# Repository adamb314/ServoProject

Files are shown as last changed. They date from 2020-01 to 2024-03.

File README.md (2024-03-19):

# ServoProject
by Adam Bäckström
### Getting the most out of your hobby servo

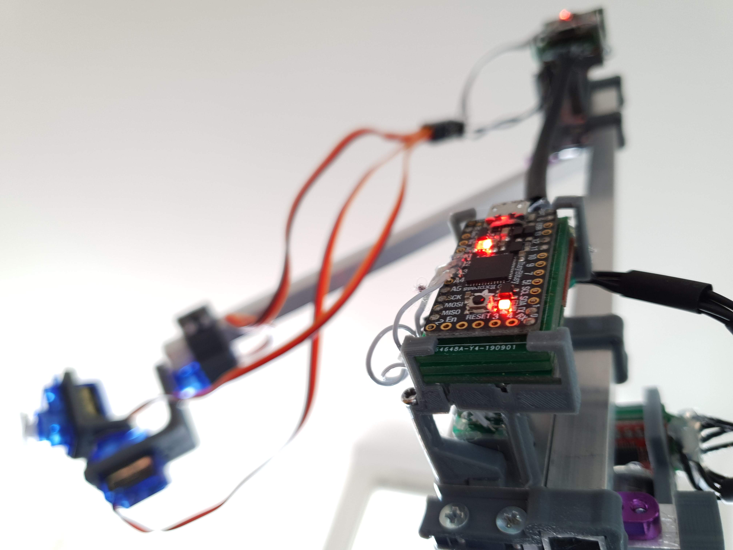
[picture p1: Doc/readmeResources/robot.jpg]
Robot


Video demo of project
---------------------

Demo video (https://www.youtube.com/watch?v=ECLrLupFW10)

Additional documentation for the project
----------------------------------------

[Theory](Doc/Theory.md)

[Dependencies](Doc/Dependencies.md)

#### Build instructions

 * [DS3225 Servo](Doc/BuildInstructionsServoDS3225.md)

 * [MG90S Micro servo](Doc/BuildInstructionsMicroServoMG90S.md)

 * [Part list for robot and gripper](Doc/PartListForRobotAndGripper.md)

 #### Legacy build instructions

   * [Brushed servo](Doc/legacy/BuildInstructionsBrushedServo.md)

   * [Coreless servo](Doc/legacy/BuildInstructionsCorelessServo.md)

   * [Micro servo](Doc/legacy/BuildInstructionsMicroServo.md)

Project structure
----------------

### ArduinoSketch

This folder contains the Arduino project for the Adafruit ItsyBitsy M0 Express boards.

Easiest way to program and configure the servos is through the configurationWizard.py script.
Just run `python3 ./ArduinoSketch/configurationWizard.py` to get started. The script will ask if it should install any missing dependencies.

PLEASE NOTE!
Windows users must use MSYS2 due to the the PyGObject package, see https://pygobject.readthedocs.io/en/latest/getting_started.html. After installing MSYS2 run the script with:
```
C:\msys64\mingw64\bin\python.exe ArduinoSketch\configurationWizard.py
```

#### Manually compiling the Arduino sketch

When compiling, the active configuration is selected by modifying the `#include "*.h"` line in the `config/config.h` file to include the desired config file. The `configSelector.py` script can be used to simplify the config selecting process by giving a drop-down list with all configs in the config folder.

The folder also holds a Makefile which can be used to compile and transfer the project. One benefit of using the Makefile is that the configSelector script is always executed prior to compiling. To be able to use the Makefile you must first install arduino-cli.

```
Arduino sketch dependencies:
  - Adafruit DotStar `source:` Arduino Library List
  - Eigen `source:` Arduino Library List
```

### ArduinoLibrary/ServoProjectController

Arduino library for communicating with the servos.

[View Example Arduino sketch](ArduinoLibrary/ServoProjectController/examples/ArduinoDemo/ArduinoDemo.ino)

### C++/Library

Holds the C++ library for communicating with the servos.
```
Dependencies:
  - GNU Make >= 4.2.1
  - gcc >= 9.3.0
  - boost >= 1.71.0
```

#### C++/Demo

Minimal c++ demo project.

[View Example Code](C++/Demo/src/main.cpp)

#### C++/Example6dofRobot

Example 6dof robot project.

[View Example Code](C++/Example6dofRobot/src/main.cpp)

To compile run `make`. This creates the program `./executable` with the following options.

```
Allowed options:
  --playPath            play the path defined in createPath()
  --gui                 open jogging gui
  --output arg          data output file
  --simulate            simulate servos

```
```
Dependencies:
  - Eigen >= 3.4.0
  - gtkmm-3.0 >= 3.24
```

### CadFiles

Holds all `.stl` and the original Freecad files

### PcbDesignes

Holds all KiCad projects for the electronics

### Python/Demo

Python demo project.

[View Example Code](Python/demo.py)

### Python/ServoProjectModules

Holds all python modules for the project.

Communication bus setup for demo projects
-----------------------------------------

#### ONLY CONNECT THE SERVO TO 3.3V LOGIC!!!!

Robot

PLEASE NOTE! The bus controller needs to have a low latency to get fast communication with the servos. Most standard USB to Serial converters buffer the data and only transfers every 10 ms or so. This becomes a problem since the communication protocol will wait for the response from each servo before moving on to the next, adding huge delays.

To get the best communication speed it is recommended to use an "Adafruit ItsyBitsy M0 Express" (or similar ARM based Arduino) as the USB to Serial converter. Just program the Arduino with the `usbToSerial.h` configuration in the ArduinoSketch to get started. In `usbToSerial.h` you can also configure any regular servos you want to control together with the ServoProject modified ones.

How to switch to PWM interface version
--------------------------------------

#### ONLY CONNECT THE SERVO TO 3.3V LOGIC!!!!

Using the PWM interface is not recommended due to low resolution and high noise, but it is possible by modifying the configuration file. To enable PWM control replace the `getCommunicationHandler()` function with the version below.

```
    static std::unique_ptr<Communication> getCommunicationHandler()
    {
        Serial.begin(115200);
        auto com = std::make_unique<Communication>(SerialComOptimizer(&Serial));
        uint8_t pwmPin = 0; // Rx pin, ONLY CONNECT TO 3.3V LOGIC!!!!
        uint8_t controlSpeed = 14;
        uint8_t backlashControlSpeed = 2;
        float scale = 2.0f; // 2 units per us (4096 units == 360 deg)
        float offset = 1024.0f; // move to 1024 units (90 deg) for 1500 us pwm signal
        com->addCommunicationNode(
                std::make_unique<DCServoCommunicationHandlerWithPwmInterface>(1,
                    createDCServo<SetupConfigHolder>(controlSpeed, backlashControlSpeed),
                    pwmPin, scale, offset));
        return com;
    }
```

License
-------

Open Source License

ServoProject is free software. You can redistribute it and/or modify it under the terms of Creative Commons Attribution 3.0 United States License.

To view a copy of this license, visit
http://creativecommons.org/licenses/by/3.0/us/

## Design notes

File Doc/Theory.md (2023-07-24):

Theory
------

## PID vs Cascade control

The control system of a regular hobby servo looks something like this:

loop1

This control scheme is good at holding and moving fast between position, but not so good at following a smooth predefined motion. Which is what you want when you build a robot.

Industrial servo controllers use a cascade based control scheme instead, which looks something like this:

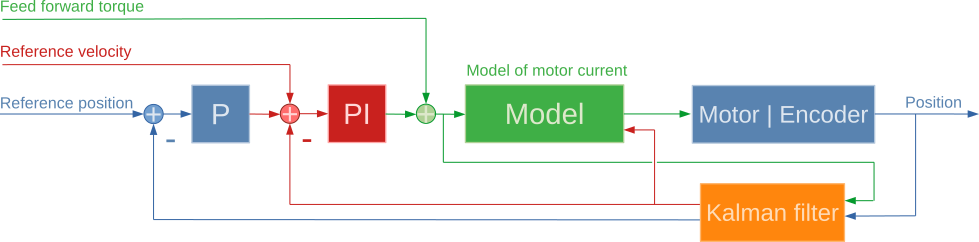
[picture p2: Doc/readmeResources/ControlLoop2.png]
loop2


This is the control scheme used in this project.

The main benefit of this approach is that it also takes the velocity and torque into account. This allows for a much tighter motion tracking.

## Backlash control

When dealing with cheap gearboxes, backlash is always a problem. The hacked servos in this project uses two encoders to compensate for backlash. One AS5048a magnetic encoder or a potentiometer on the output shaft and one custom optical encoder inside the DC-motor. The benefit of having the extra encoder inside the motor is getting higher resolution and a main control loop which is backlash free. If one would only use the AS5048a for controlling, the backlash would enter the control loop as a time delay. This limits the control loop performance.

The backlash compensation is done by moving the motor position control loops reference-position so that the output encoder reaches the correct position.

## The complete control loop

The following diagram shows the full control loop design used in this project:

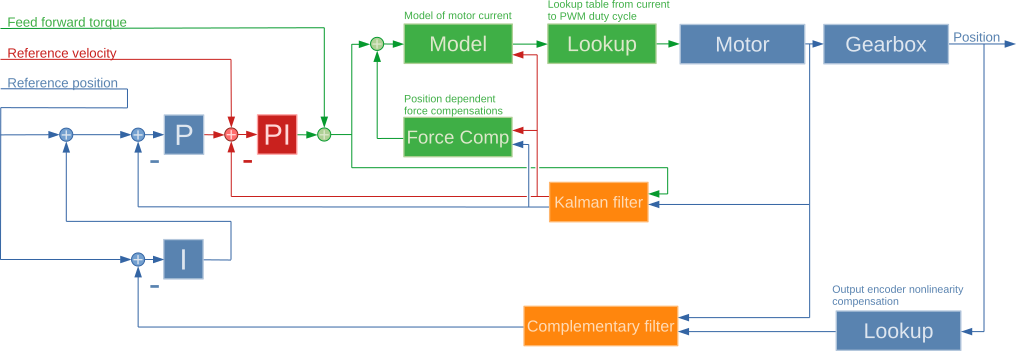
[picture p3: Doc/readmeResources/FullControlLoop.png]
fullLoop


It consists of three cascade control levels:
1) Backlash control loop
2) Motor position control loop
3) Motor velocity control loop

Apart from these three feedback loops there are four model/open-loop based compensation steps based on:
1) Velocity based motor current model (see CurrentControlModel class in `ArduinoSketch/src/Control/CurrentControlLoop.cpp`)
2) PWM duty cycle based motor current model (lookup table based, see `ArduinoSketch/src/Hardware/PwmHandler.cpp`)
3) Motor position based force compensation (see `ArduinoSketch/src/Control/DCServo.cpp` function `applyForceCompensations`)
4) Output encoder nonlinearity model

For the exact implementation see the `controlLoop()` function in `ArduinoSketch/src/Control/DCServo.cpp`.

## System identification

To be able to calculate the parameters of the control loops we need to have a mathematical model of the servo. This is handled by the python module `SystemIdentification.py`. First step is to record the position-time-series of the motor for a sequence of PWM values with random sign. The sequence starts with the highest PWM value, in the test range, and moves down towards the lowest, in discrete steps. Next the velocity is calculated from the position-time-series. For each part, with the same absolute PWM value, the velocity change will follow this equation:

$$ v_{k+1} = a v_k + b u_k - c_f sign(v_k) $$

where $u_k$ is $\pm$ the PWM value and $c_f$ is the friction constant. By only considering the parts where

$$ sign(v_k) = sign(u_k) $$

we can bake in $c_f$ into $b$ resulting in:

$$ v_{k+1} = a v_k + b^{'} u_k $$

The parameters $a$ and $b^{'}$ are then estimated with the least squares method. After that their continuous time equivalent values $a_{cont}$ and $b_{cont}$ are calculated.

How $b_{cont}$ varies over the PWM range is then used to calculate the PWM nonlinearity and the linear trend of $a_{cont}$ is used to calculate the $c_{EMF}$ value of the motor.

After this we add friction to the model and simulate the response. The final friction $c_{fric}$ is calculated by minimizing the error between the model and the real system.

The final model looks like this:

$$ \frac{dv}{dt} = a_{cont} v(t) + b_{cont} pwmNonlin(u(t)) + c_{fric} sign(v(t)) + c_{EMF} abs(pwmNonlin(u(t))) v(t) $$

## Calculating the control parameters
This project uses pole placement to calculate the control parameters for the cascade controllers. To get the equations for the poles we need to find the closed transfer functions for the velocity and position control loops.

### Transfer function of open system to closed system
Given the discrete transfer function for the open system:

$$ G_0(z)=\frac{p(z)}{q(z)} $$

where $p(z)$ and $q(z)$ are pure polynomials, we can derive the closed system's transfer function as follows:

$$ Y = G_0(z) (R - Y) \iff Y = \frac{G_0(z)}{1 + G_0(z)} R = \frac{p(z)}{p(z) + q(z)}R $$

Which gives us the closed system transfer function

$$ G_c(z) = \frac{p(z)}{p(z) + q(z)} $$

### Position control loop

The position control loop's open transfer function consists of a proportional gain controller and an integrator (we approximate the inner velocity loop as a pure integrator):

$$ G_0(z)=G_{posControl}(z) G_{velLoop}(z)= (L_0) (\frac{dt}{z - 1}) $$

This gives us $p(z) = L_0 dt$ and $q(z) = z - 1$ which means that the pole polynomial is:

$$ p(z) + q(z) = z - 1 + L_0 dt $$

with the root:

$$ z - 1 + L_0 dt = 0 \iff z_{posPole} = 1 - L_0 dt $$

which means that the position control loop gain $L_0$ can be calculated with:

$$ L_0 =\frac{1 - z_{posPole}}{dt} $$

### Velocity control loop

The velocity control loop's open transfer function consists of a PI controller and the motor's transfer function (from control signal to velocity) which we approximate as a first order damped system:

$$ G_0(z)=G_{velControl}(z) G_{motor}(z)= (L_1 + L_2 \frac{1}{z - 1})(\frac{b}{z - a}) $$

This gives us $p(z) = b (L_1 (z - 1) + L_2)$ and $q(z) = (z - 1)(z - a)$ which means that the pole polynomial is:

$$ p(z) + q(z) = b (L_1 (z - 1) + L_2) + (z - 1)(z - a) = (a - b L_1 + b L_2) + (b L_1 -a - 1) z + z^2 $$

Substituting in $L_1^{'} = b L_1$ and $L_2^{'} = b L_2$ gives us:

$$ (a - L_1^{'} + L_2^{'}) + (L_1^{'} -a - 1) z + z^2 $$

with the roots:

$$ z_{velPole} = 1/2 (±\sqrt{{L_1^{'}}^2 + (1 - a) ((1 - a) + 2 L_1^{'}) - 4 L_2^{'}} + a - L_1^{'} + 1) $$

Given that we want the closed loop system to be stable and at least as fast as the open loop ($z_{openLoopPole} = a$) we can deduce the following:

$$ 0 < 1/2 (a - L_1^{'} + 1) \le a \le 1  \iff $$

$$ 0 < a - L_1^{'} + 1 \le 2a, \space 0 < a \le 1 \Rightarrow $$

$$ 0 \le 1 - a \le L_1^{'} < a + 1 \le 2 $$

To get a damped system we need real roots $\Rightarrow$

$$ {L_1^{'}}^2 + (1 - a) ((1 - a) + 2 L_1^{'}) - 4 L_2^{'} \ge 0 $$

since $0 < a \le 1$ and $L_1^{'} > 0 \Rightarrow$

$$ {L_1^{'}}^2 + (1 - a) ((1 - a) + 2 L_1^{'}) - 4 L_2^{'} \ge 
 {L_1^{'}}^2 - 4 L_2^{'} \ge 0 $$

Substituting back to $L_1$ and $L_2$ results in:

$$ b (b L_1^2 - 4 b L_2) \ge 0 \iff b L_1^2 \ge 4 L_2 $$

If $L_1$ and $L_2$ are calculated so that

$$ {L_1^{'}}^2 - 4 L_2^{'} = 0 $$

then an increase of the load inertial on the motor ($b^{'} < b$) will result in an undamped system. To prevent this we can introduce an inertial margin $c_{im}$ such that $b^{'} = b / c_{im} \le b$. We want the damped system inequality to hit the limit if $b$ changes to $b^{'}$. This yields the following:

$$ (a - 1)^2 - 2 a L_1^{'} / c_{im} + (L_1^{'} / c_{im})^2 + 2 L_1^{'} / c_{im} - 4 L_2^{'} / c_{im} = 0 \iff $$

$$ L_2^{'} = 1/4 (c_{im} (a - 1)^2 - 2 a L_1^{'} + {L_1^{'}}^2 / c_{im} + 2 L_1^{'}) = $$

$$ = L_2^{'} = 1/4 ({L_1^{'}}^2 / c_{im} + (a - 1) (c_{im} (a - 1) - 2 L_1^{'})) $$

The slowest pole of a system is the one that affect the speed of the system the most and a discrete pole is slower the closer to the value one it is. Since both of the velocity poles should satisfy

$$ 0 < z_{velPole} \le a $$

we should place the largest pole of the two:

$$ z_{velPole} = 1/2 (\sqrt{{L_1^{'}}^2 + (1 - a) ((1 - a) + 2 L_1^{'}) - 4 L_2^{'}} + a - L_1^{'} + 1) $$

substituting in $L_2^{'}$

$$ z_{velPole} = 1/2 (\sqrt{{L_1^{'}}^2 + (1 - a) ((1 - a) + 2 L_1^{'}) - {L_1^{'}}^2 / c_{im} - (1 - a) (c_{im} (1 - a) + 2 L_1^{'})} + a - L_1^{'} + 1) = $$

$$ = z_{velPole} = 1/2 (\sqrt{(1 - 1 / c_{im}) {L_1^{'}}^2 + (1 - a) ((1 - a) + 2 L_1^{'} - c_{im} (1 - a) - 2 L_1^{'})} + a - L_1^{'} + 1) = $$

$$ = z_{velPole} = 1/2 (\sqrt{(1 - 1 / c_{im}) {L_1^{'}}^2 + (1 - a)^2 (1- c_{im})} + a - L_1^{'} + 1) \Rightarrow $$

$$ L_1^{'} = c_{im} (a - 2 z_{velPole} + 1) + 2 \sqrt{c_{im} (c_{im} - 1) (1 - z_{velPole}) (a - z_{velPole})} $$

Resulting in the final equations:

$$ L_1^{'} = c_{im} (a - 2 z_{velPole} + 1) + 2 \sqrt{c_{im} (c_{im} - 1) (1 - z_{velPole}) (a - z_{velPole})} $$

$$ L_2^{'} = 1/4 ({L_1^{'}}^2 / c_{im} + (a - 1) (c_{im} (a - 1) - 2 L_1^{'})) $$

$$ L_1 = L_1^{'} / b $$

$$ L_2 = L_2^{'} / b $$

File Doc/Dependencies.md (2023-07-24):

Dependencies
------------

#### ArduinoSketch/configSelector.py
* Python >= 3.8.2
* python3-gi

#### ArduinoSketch/configurationWizard.py
* Python >= 3.8.2
* python3-gi

* matplotlib >= 3.4.2
* numpy >= 1.17.4
* pyserial >= 3.5
* requests >= 2.22.0
* scipy >= 1.7.0

#### ArduinoSketch/Makefile
* GNU Make >= 4.2.1
* arduino-cli

#### C++/Demo
* GNU Make >= 4.2.1
* gcc >= 9.3.0
* boost >= 1.71.0

#### C++/Example6dofRobot
* GNU Make >= 4.2.1
* gcc >= 9.3.0
* boost >= 1.71.0
* Eigen >= 3.4.0
* gtkmm-3.0 >= 3.24

#### C++/Library
* GNU Make >= 4.2.1
* gcc >= 9.3.0
* boost >= 1.71.0

#### Python/demo.py
* Python >= 3.8.2
* numpy >= 1.17.4
* pyserial >= 3.5

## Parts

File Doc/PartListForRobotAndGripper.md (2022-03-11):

Gripper
--------

* 1 x SG90 servo

".stl" files for 3D printing:
```
CadFiles/Robot/stl/GripperBase.stl
CadFiles/Robot/stl/GripperClip.stl
CadFiles/Robot/stl/GripperFinger1.stl
CadFiles/Robot/stl/GripperFinger2.stl
CadFiles/Robot/stl/GripperMount.stl
```

Robot
--------

* 3 x Modified coreless servo
* 3 x Modified micro servo
* 1 x Gripper
* 1 x 10 x 10 mm square aluminum bar (about 500 mm)
* 1 x 15 x 15 mm square aluminum bar (about 100 mm)
* 1 x 5V Powersuply 
* 1 x Fast USB to serial microcontroller (Adafruit ItsyBitsy M0 Express or Arduino MKR Zero)
  * https://learn.adafruit.com/introducing-itsy-bitsy-m0
  * https://store.arduino.cc/arduino-mkr-zero-i2s-bus-sd-for-sound-music-digital-audio-data

Cad and stl files for 3D printing:
```
CadFiles/Robot
```

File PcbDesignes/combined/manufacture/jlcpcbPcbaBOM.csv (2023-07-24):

Comment | Designator | Footprint | LCSC Part #
10uF | C1 C3 |  | C15525
1uF | C4 C5 |  | C52923
LED | D1 |  | C84256
D | D2 D3 |  | C64898
120 | R1 R2 |  | C25079
8.2k | R3 R5 |  | C25924
100k | R4 |  | C25741
2.2k | R6 |  | C25924
AP2112K-3.3 | U3 |  | C51118
ATSAMD21G18A-A | U4 |  | C78624
TB6612FNG | U5 |  | C88224
USB_B_Micro | USB1 |  | C132563

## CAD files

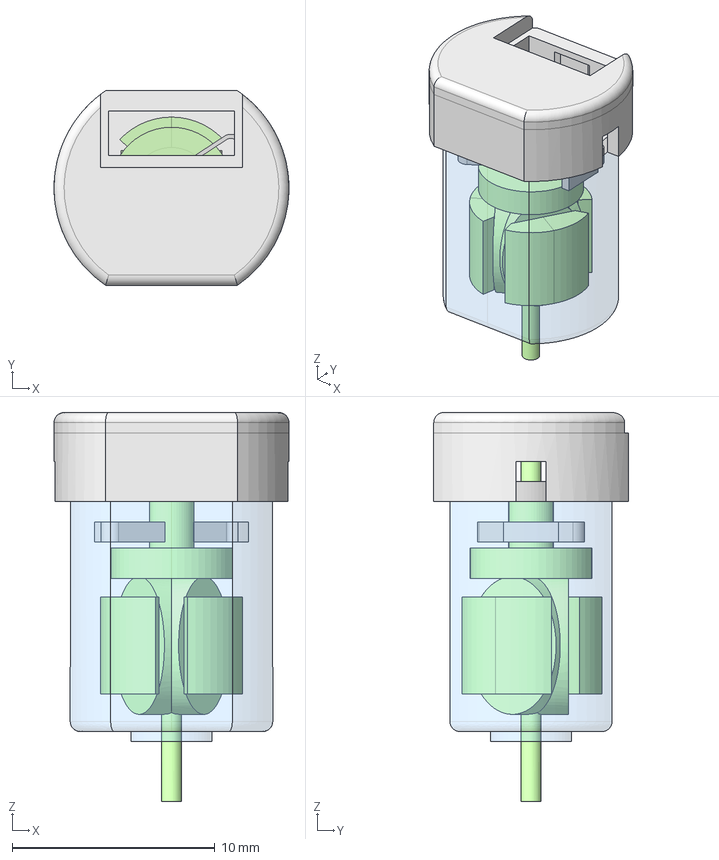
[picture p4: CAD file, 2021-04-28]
CadFiles/MicroServo/MicroServoAssembly.FCStd
11.6 x 9.60 x 19.2 mm
sensorMount

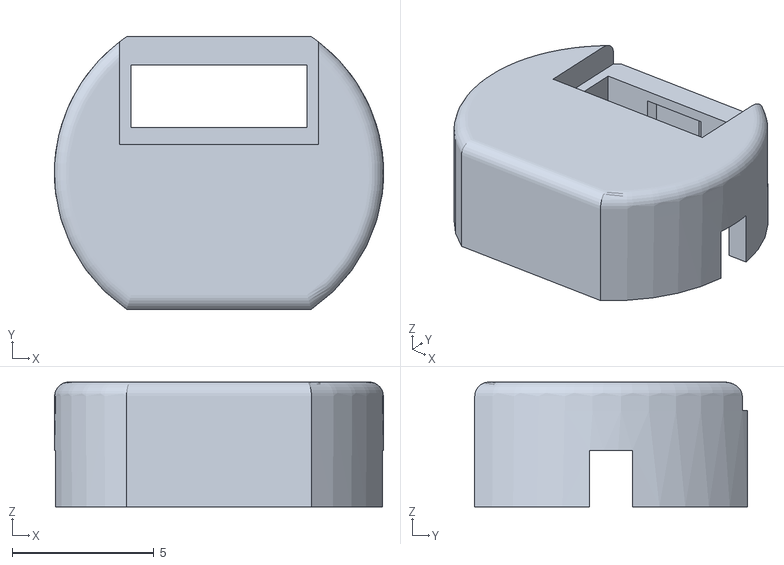
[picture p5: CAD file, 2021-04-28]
CadFiles/MicroServo/stl/OpticalEncoderSensorMount.stl
11.6 x 9.60 x 4.40

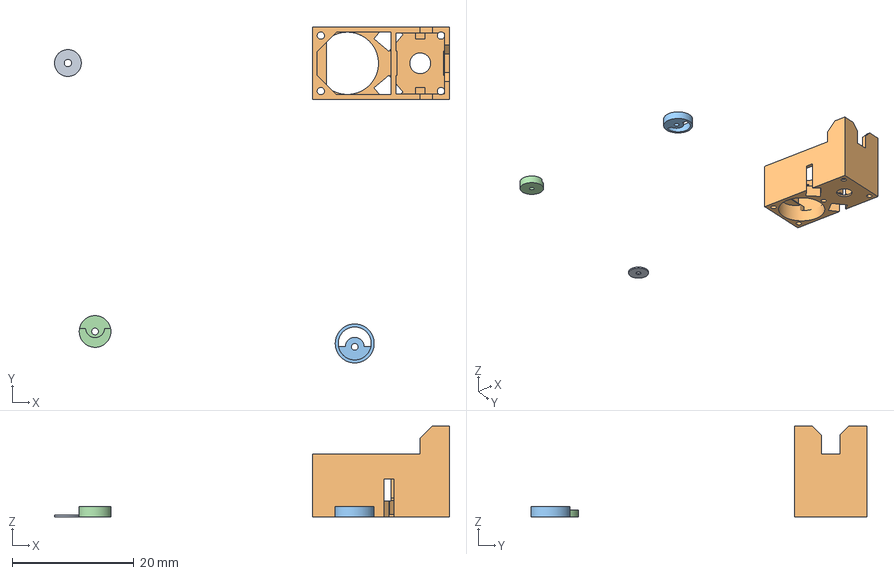
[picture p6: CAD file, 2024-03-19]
CadFiles/MicroServoMG90S/prusaSlicer.3mf
64.8 x 55.1 x 14.9 mm
baseBushings.stl
baseBox.stl
encDisc(white).stl
encDiscTruningMount(white).stl

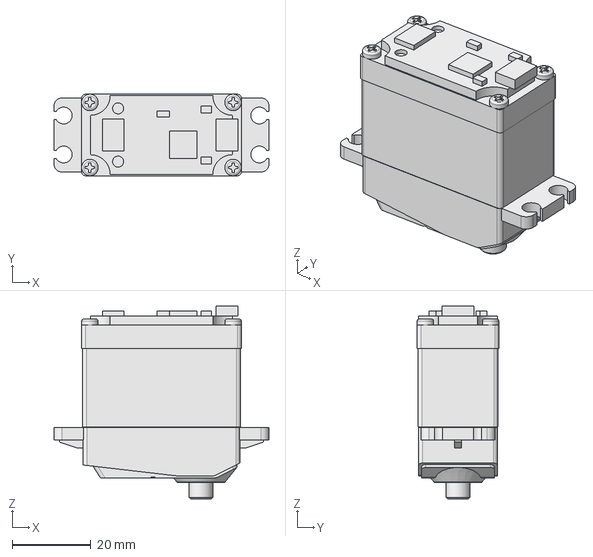
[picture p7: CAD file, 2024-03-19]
CadFiles/Robot/brushedServo.step
54.5 x 20.7 x 48.9 mm

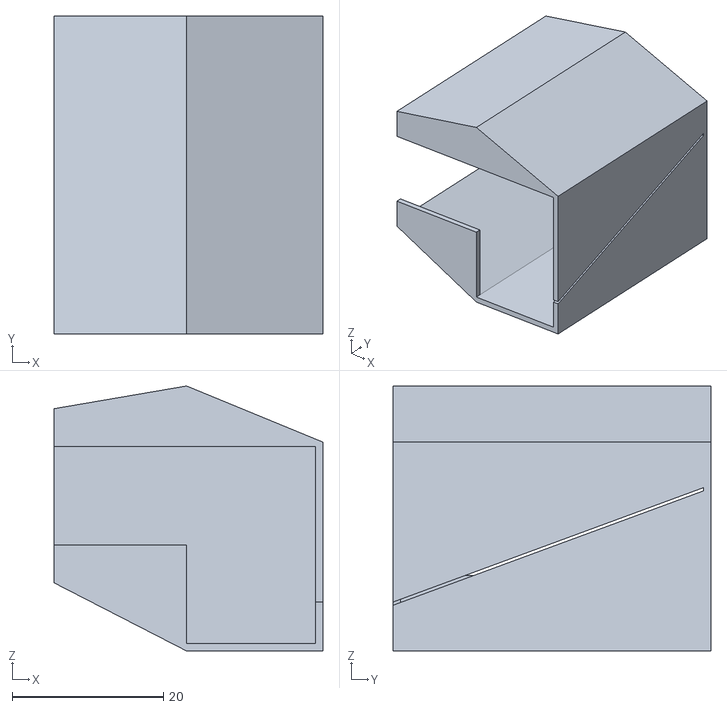
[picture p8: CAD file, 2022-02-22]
CadFiles/Robot/stl/s3Cover.stl
35.5 x 42.0 x 35.0

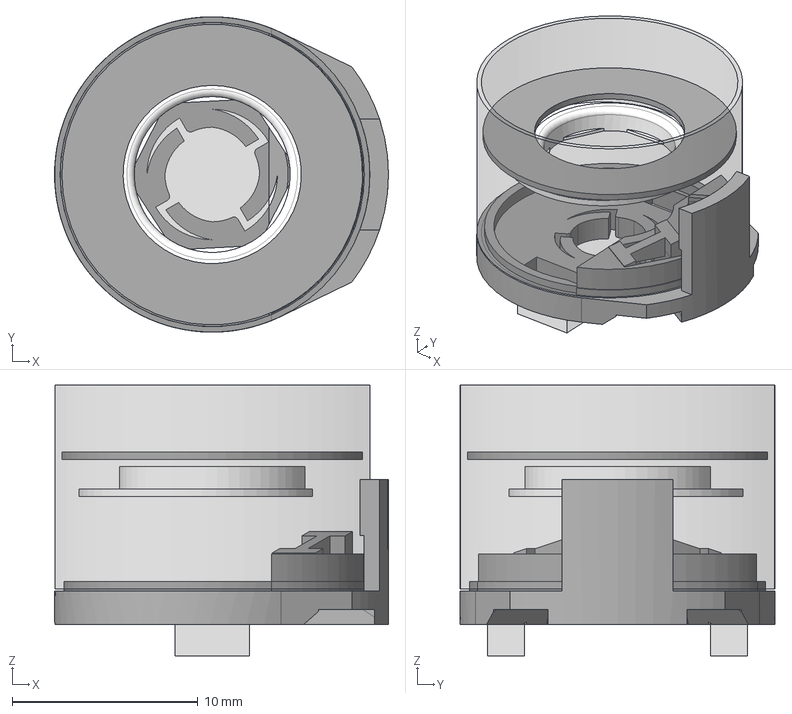
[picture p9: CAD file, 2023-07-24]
CadFiles/ServoBrushed/motor.FCStd
18.0 x 17.0 x 14.6 mm
motorPart1
motorPart2
sensor1
sensor2
EncoderDiscWhite
EncoderDiscBlack
MotorLid

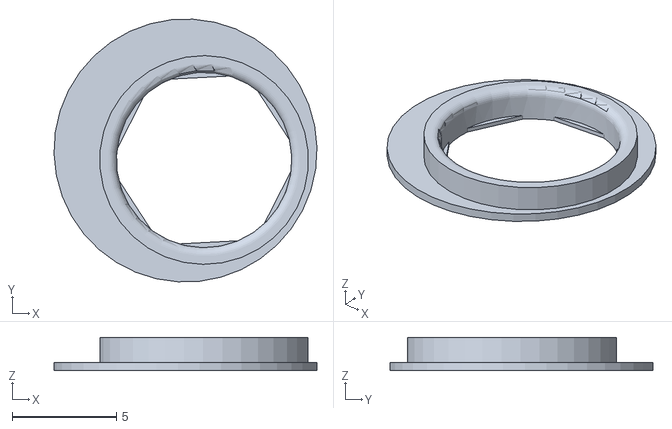
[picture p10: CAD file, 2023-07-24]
CadFiles/ServoBrushed/stl/EncDiscWhite.stl
12.6 x 12.6 x 1.60

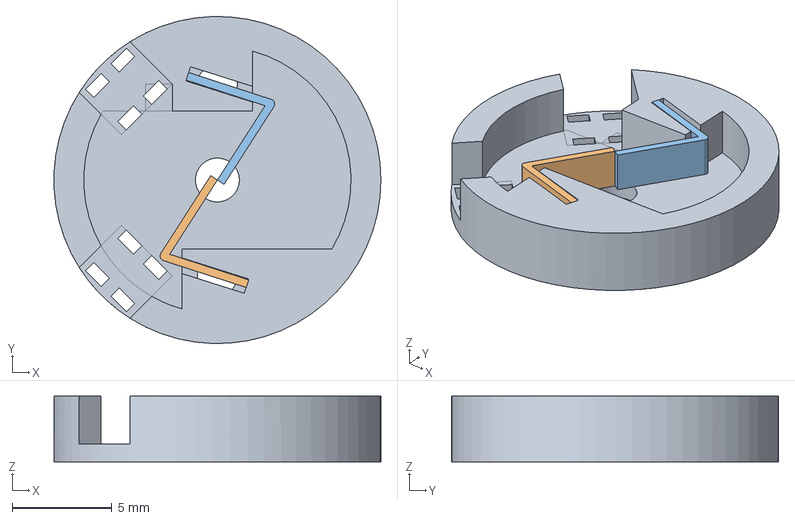
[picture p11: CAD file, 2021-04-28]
CadFiles/ServoCoreless/motorLid.FCStd
16.4 x 16.4 x 3.30 mm
Lid

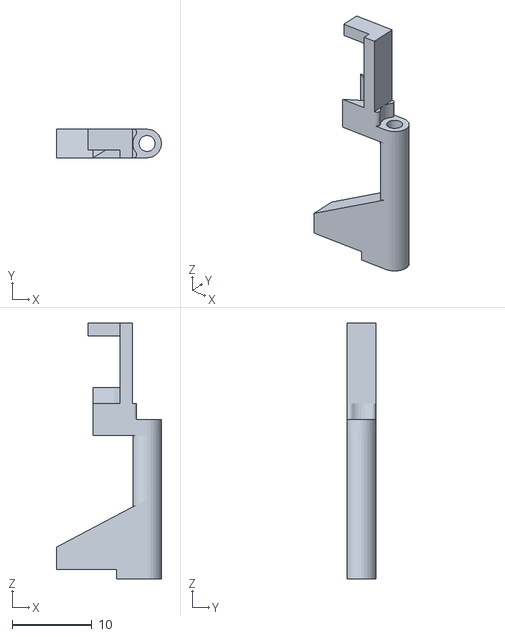
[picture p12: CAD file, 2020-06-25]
CadFiles/ServoCoreless/stl/pcbMount-part3.stl
13.2 x 3.60 x 32.1

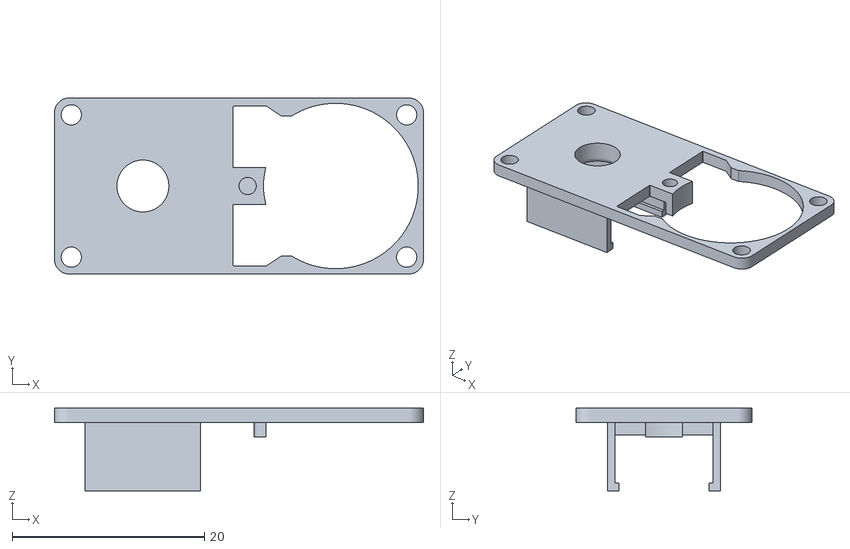
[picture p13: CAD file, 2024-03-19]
CadFiles/ServoDS3225/gearLidBottom.stl
38.4 x 18.3 x 8.60

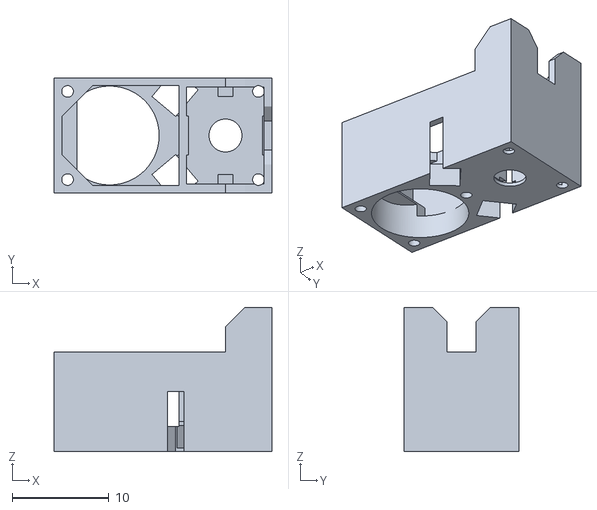
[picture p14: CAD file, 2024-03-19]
CadFiles/MicroServoMG90S/baseBox.stl
22.5 x 11.9 x 14.9

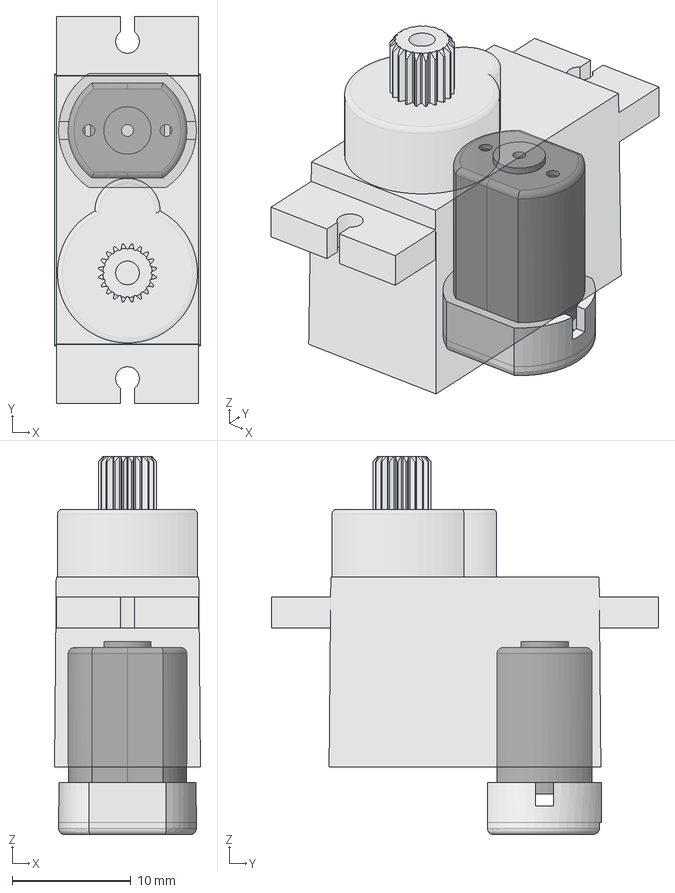
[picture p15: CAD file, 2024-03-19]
CadFiles/Robot/microServo.step
12.3 x 32.6 x 31.9 mm

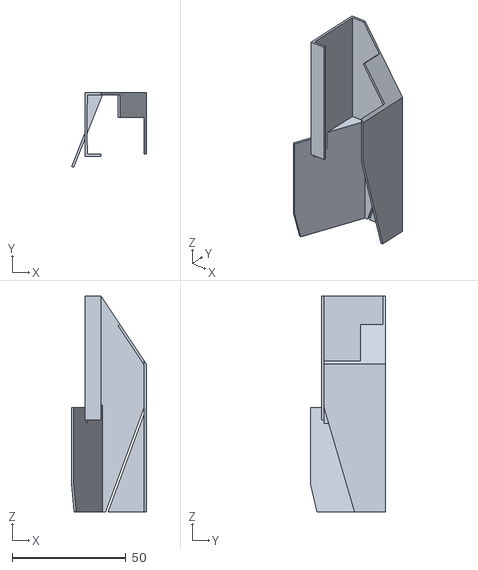
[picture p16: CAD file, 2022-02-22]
CadFiles/Robot/stl/s4Cover.stl
32.9 x 32.9 x 95.0

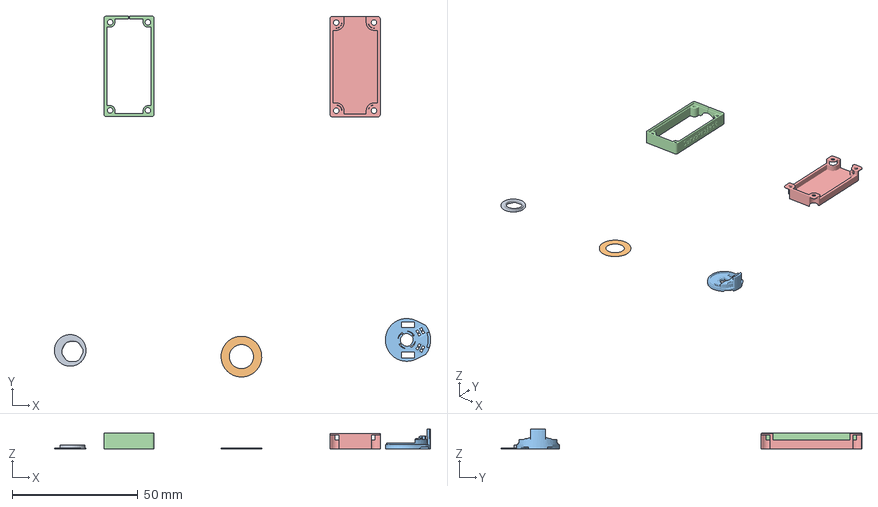
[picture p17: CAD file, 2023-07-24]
CadFiles/ServoBrushed/PrusaMiniPrintProject.3mf
149.5 x 143.4 x 7.80 mm
EncDiscWhite.stl
EncDiscBlack.stl
motorLid.stl
backCover.stl
backCoverTransparent.stl

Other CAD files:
CadFiles/ServoBrushed/stl/motorLid.stl
CadFiles/ServoCoreless/pcbMount.FCStd
CadFiles/ServoCoreless/stl/pcbMount-part2.stl
CadFiles/ServoDS3225/pcbMount.stl
CadFiles/MicroServoMG90S/baseBushings.stl
CadFiles/MicroServoMG90S/encDisc.stl
CadFiles/MicroServoMG90S/encDiscTruningMount.stl
CadFiles/Robot/brushedServoHorn.step
CadFiles/Robot/stl/GripperBase.stl
CadFiles/Robot/stl/GripperClip.stl
CadFiles/Robot/stl/GripperFinger1.stl
CadFiles/Robot/stl/GripperFinger2.stl
CadFiles/Robot/stl/GripperMount.stl
CadFiles/Robot/stl/ServoBigMagEnc.stl
CadFiles/Robot/stl/ServoBigMagEncMagHold.stl
CadFiles/Robot/stl/ServoBigMount.stl
CadFiles/Robot/stl/ServoBigMountMirrored.stl
CadFiles/Robot/stl/midS2S3Cover.stl
CadFiles/Robot/stl/s1Cover.stl
CadFiles/Robot/stl/s4Bushing.stl
CadFiles/Robot/stl/s4Mount.stl
CadFiles/Robot/stl/s5Bushing.stl
CadFiles/Robot/stl/s5Cover.stl
CadFiles/Robot/stl/s5CoverP2.stl
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

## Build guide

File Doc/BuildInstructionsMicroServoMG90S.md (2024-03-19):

## Part list

* WS-MG90S micro servo
* 2 x ITR8307
* Custom PCB
* Flat cables
    * 2 leads wide
    * 3 x 3 leads wide
    * 4 leads wide
* pin header 1x4
* 3D printed parts
    * baseBox
    * baseBushing
    * encDisc
    * encDiscTurningMount

## Build instructions

### Prepare parts

1. Order PCB using gerber, BOM and CPL files:
    - `PcbDesignes/combined/manufacture/gerber.zip`
    - `PcbDesignes/combined/manufacture/jlcpcbPcbaBOM.csv`
    - `PcbDesignes/combined/manufacture/jlcpcbPcbaCPL.csv`

2. Burn bootloader to PCB with a Raspberry Pi

    Power PCB via USB from pi and connect:
    ```
        Prog1:D (swdio) -> GPIO 25
        Prog1:C (swclk) -> GPIO 11
        Prog1:Reset     -> 3.3v

        (GPIO nr are for a Raspberry Pi 3 B)
    ```

     1. Install OpenOCD on the pi with this guide:
           https://learn.adafruit.com/programming-microcontrollers-using-openocd-on-raspberry-pi/compiling-openocd
        
        or using apt-get:
        ```
           sudo apt-get install openocd
        ```
    
     2. Download bootloader:
           https://github.com/adafruit/uf2-samdx1/releases/download/v3.13.0/bootloader-itsybitsy_m0-v3.13.0.bin
    
        or latest from:
           https://github.com/adafruit/uf2-samdx1/releases
          
     3. Put \*.bin file in new folder on pi together with the file [burnBootloaderWithOpenOCD.txt](../PcbDesignes/burnBootloaderWithOpenOCD.txt) and rename the script file to `openocd.cfg`

     4. run:
        ```
           cd \\|Insert name of folder on pi with the script
           sudo openocd
        ```

3. Print objects in PrusaSlicer project file `CadFiles/MicroServoMG90S/prusaSlicer.3mf`
    
    Print in black PLA:
    - `baseBox.stl`
    - `baseBushings.stl`

    Print in white PLA:
    - `encDisc.stl`
    - `encDiscTurningMount.stl`

### Modify the servo

Modify the servo according to the [Build Video](https://youtu.be/VcU6IY8n05g?t=0)

Build Video (https://youtu.be/VcU6IY8n05g?t=0)

Build steps in video:

1. Disassemble the servo

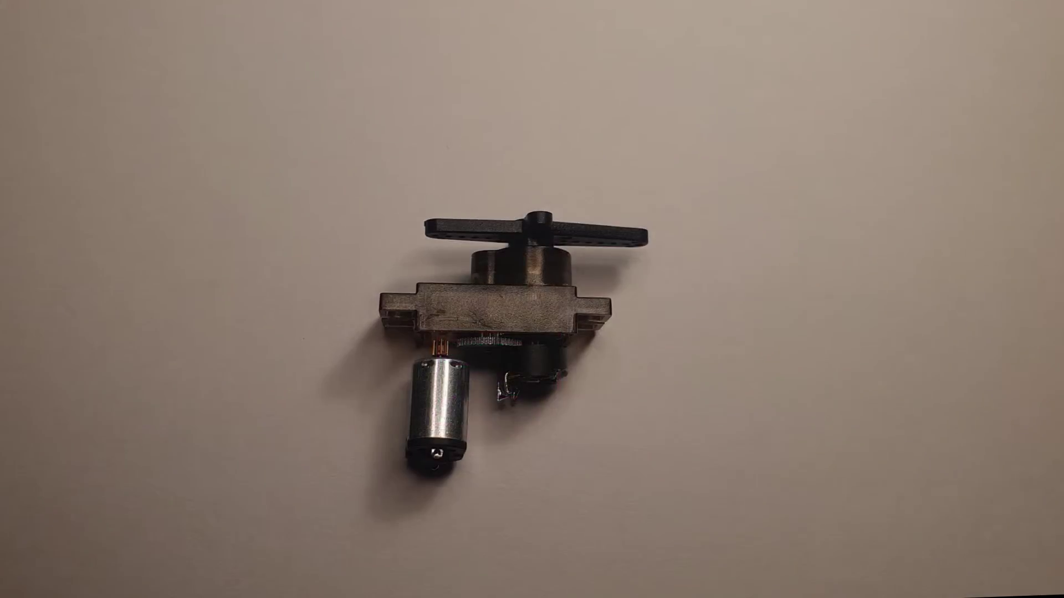
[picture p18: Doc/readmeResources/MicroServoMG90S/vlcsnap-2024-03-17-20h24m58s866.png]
    

2. The `encDisc` part has to  be completely smooth and free from defects. Getting the required resolution out of a normal FDM 3D printer is basically impossible. So to get a smooth `encDisc` part we first need to file it down while spinning it:

    1. Remove the gear from the motor and mount `encDiscTurningMount` on motor axis. Then mount `encDisc` on `encDiscTurningMount`

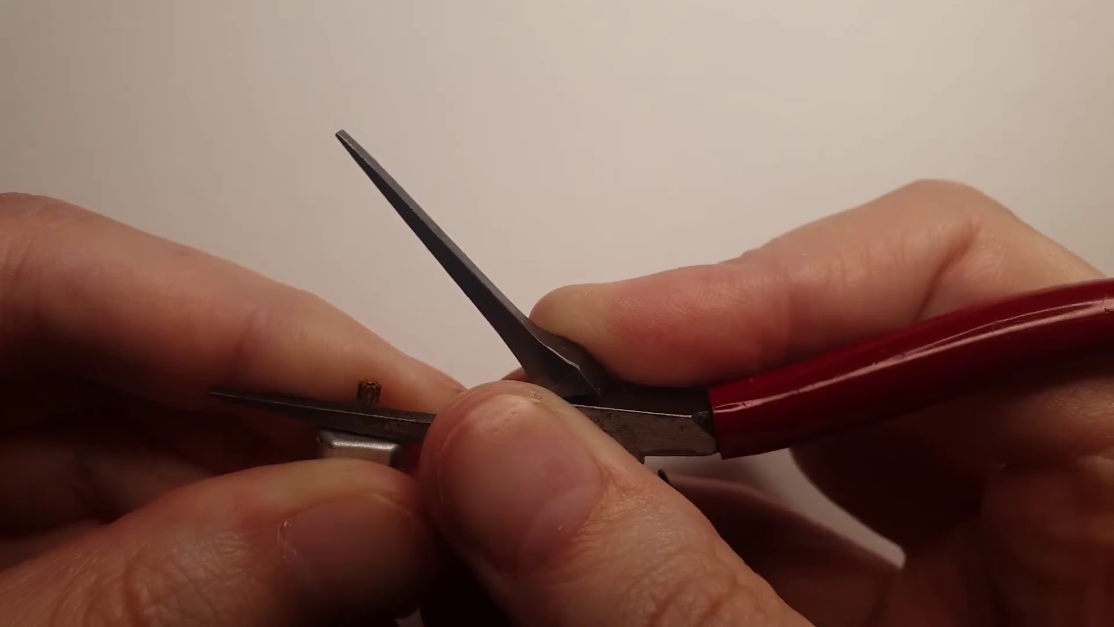
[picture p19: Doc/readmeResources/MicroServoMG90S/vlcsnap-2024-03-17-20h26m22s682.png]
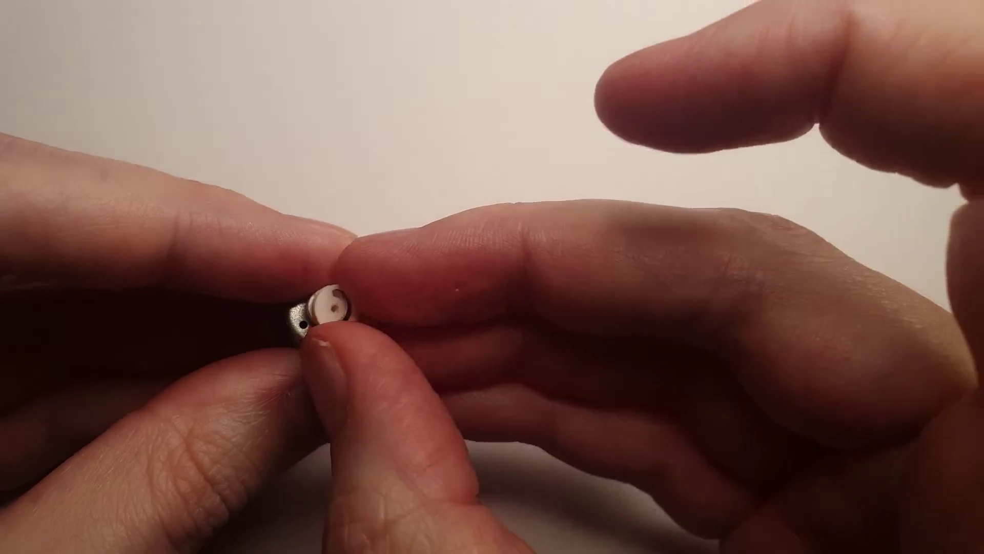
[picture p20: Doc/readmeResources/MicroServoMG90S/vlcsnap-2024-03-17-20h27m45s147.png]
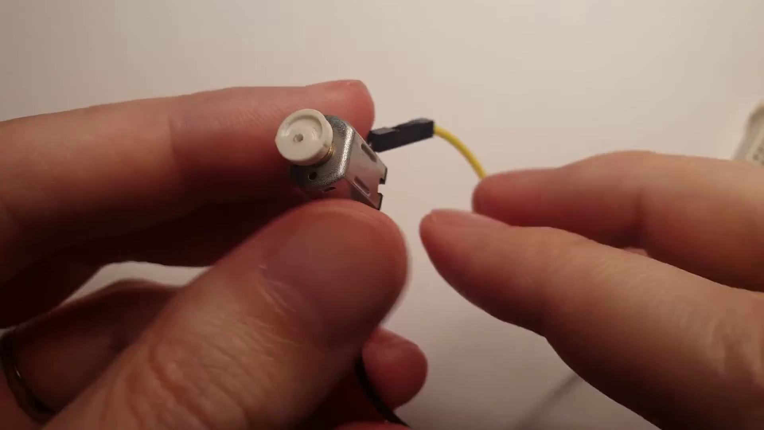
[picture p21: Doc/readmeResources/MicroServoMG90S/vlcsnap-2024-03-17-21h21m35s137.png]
          

    2. Apply 3-5 volts to the motor and file down 3D printing seams and printing lines until the surface of `encDisc` is completely smooth

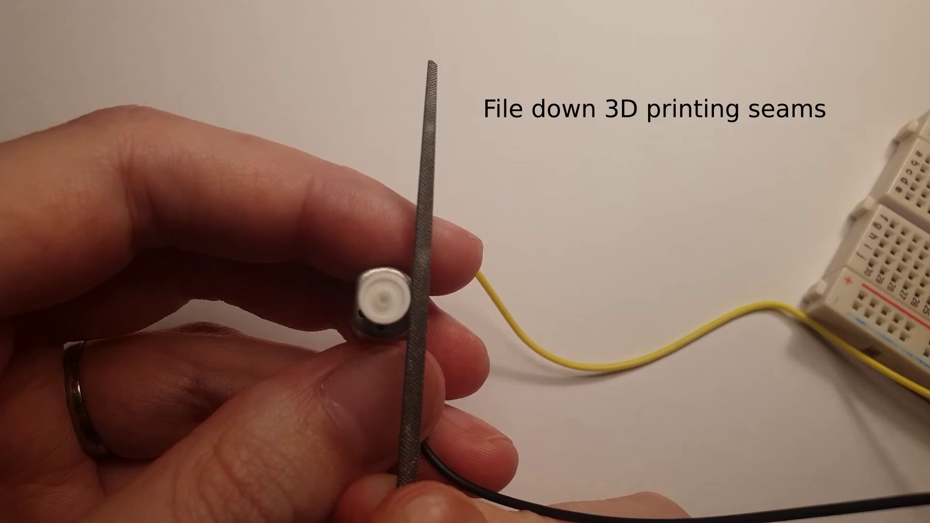
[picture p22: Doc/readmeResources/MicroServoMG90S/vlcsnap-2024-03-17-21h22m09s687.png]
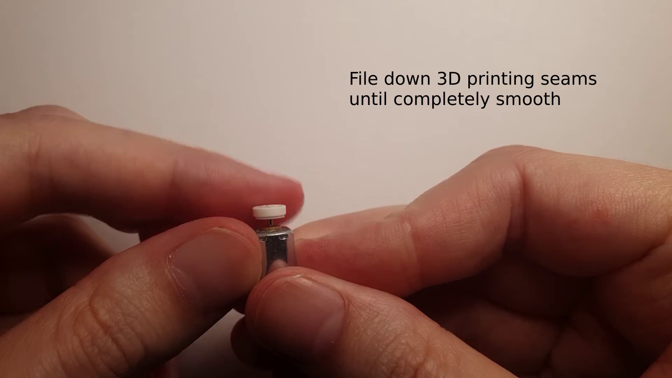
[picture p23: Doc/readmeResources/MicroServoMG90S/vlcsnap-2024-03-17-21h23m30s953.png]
         

3. Mount the smooth `encDisc` and gear on the motor axis

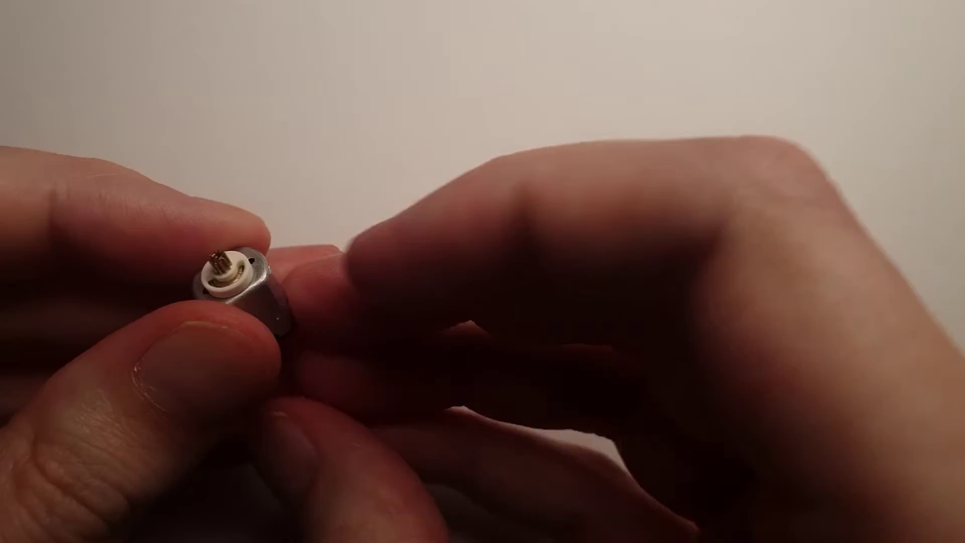
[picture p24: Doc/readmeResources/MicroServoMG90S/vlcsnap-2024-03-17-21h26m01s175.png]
    

4. Solder on a 3 lead wide flat cable to each of the two ITR8307 sensors. Make sure that the orientation of the sensors are mirrored

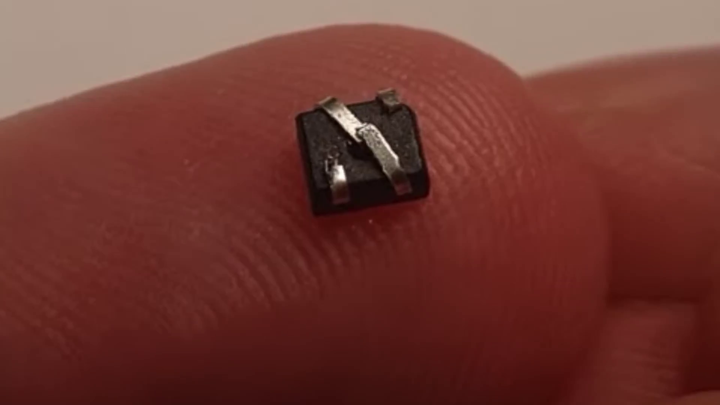
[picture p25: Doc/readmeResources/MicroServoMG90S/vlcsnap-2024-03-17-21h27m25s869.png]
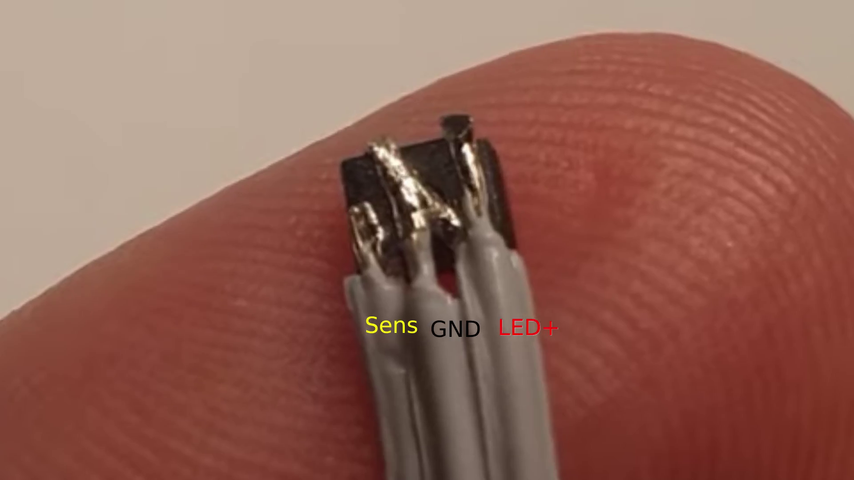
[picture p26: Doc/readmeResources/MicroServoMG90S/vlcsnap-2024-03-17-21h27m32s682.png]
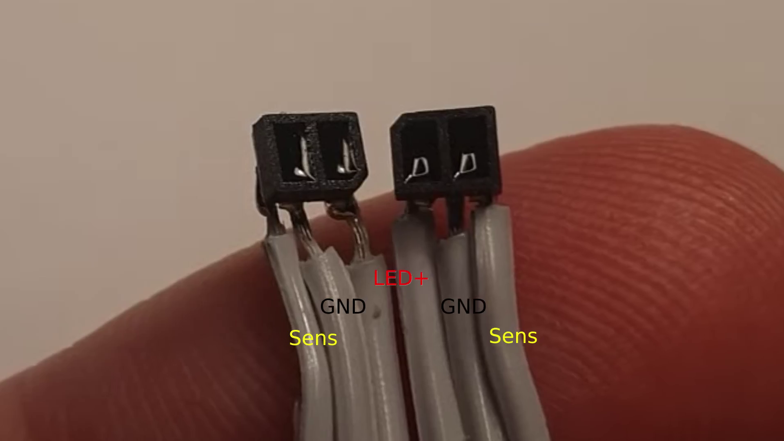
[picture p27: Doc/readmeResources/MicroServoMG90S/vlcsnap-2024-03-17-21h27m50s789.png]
      

5. Mount the sensors in `baseBox` so that the LED segment (pin 1) of the sensors are oriented towards each other

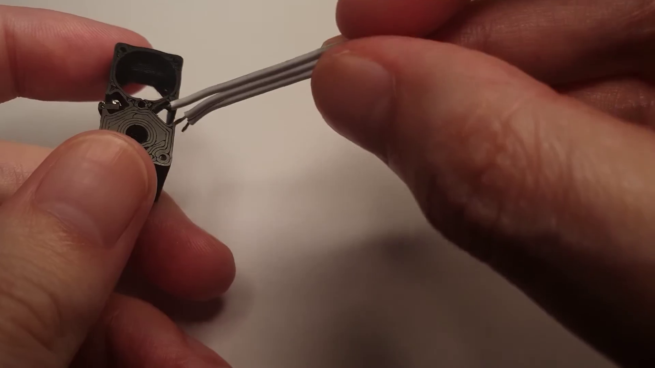
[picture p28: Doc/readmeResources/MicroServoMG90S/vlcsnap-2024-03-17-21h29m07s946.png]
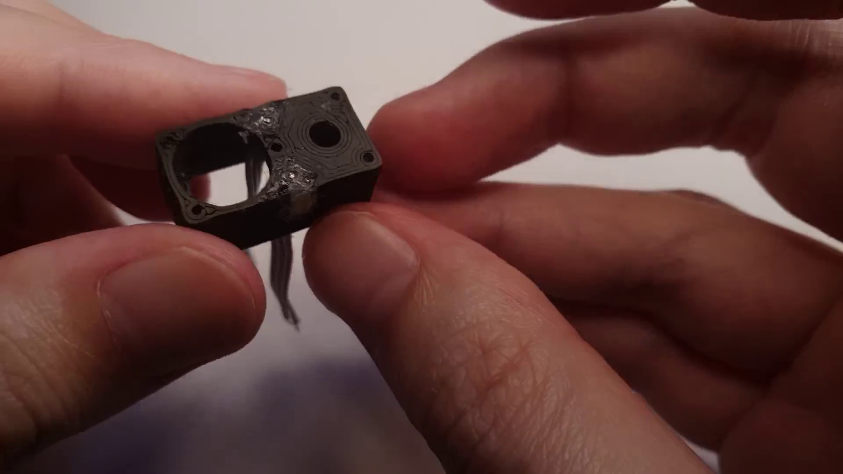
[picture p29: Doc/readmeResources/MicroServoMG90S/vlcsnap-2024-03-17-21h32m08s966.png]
     

6. Solder the ITR8307 sensors and potentiometer to the PCB

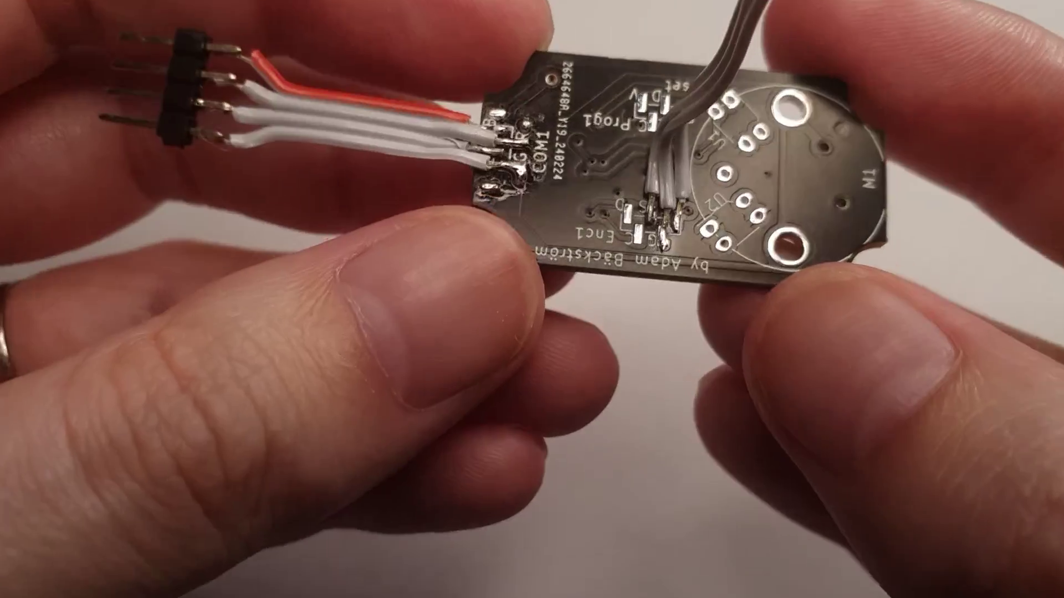
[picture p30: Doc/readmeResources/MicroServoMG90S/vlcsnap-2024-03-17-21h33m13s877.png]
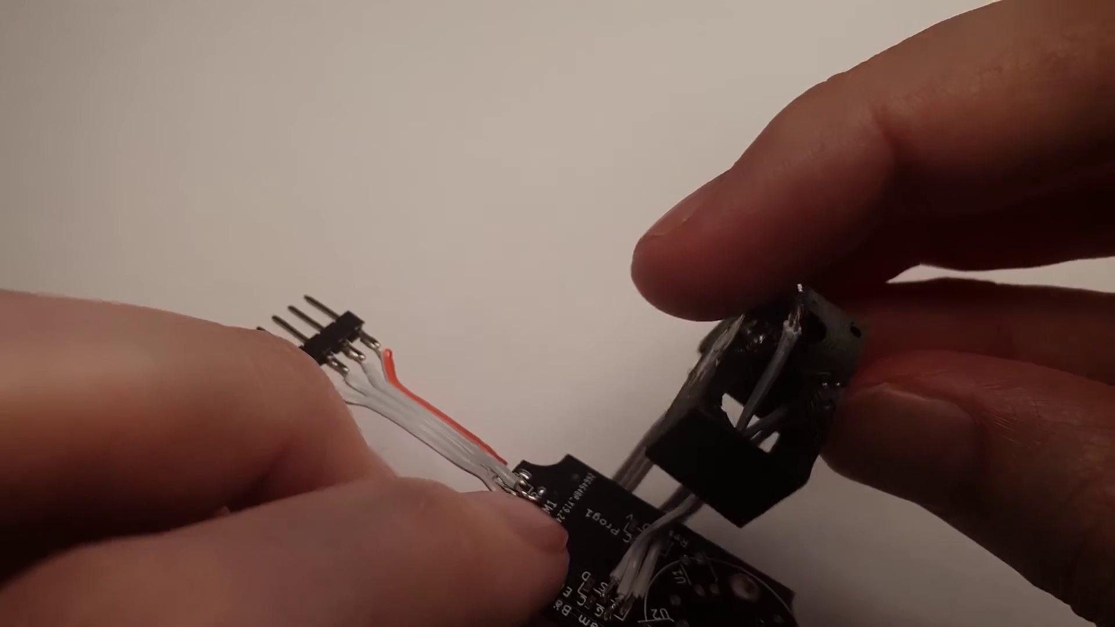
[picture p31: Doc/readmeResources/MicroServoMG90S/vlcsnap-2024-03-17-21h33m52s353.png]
     
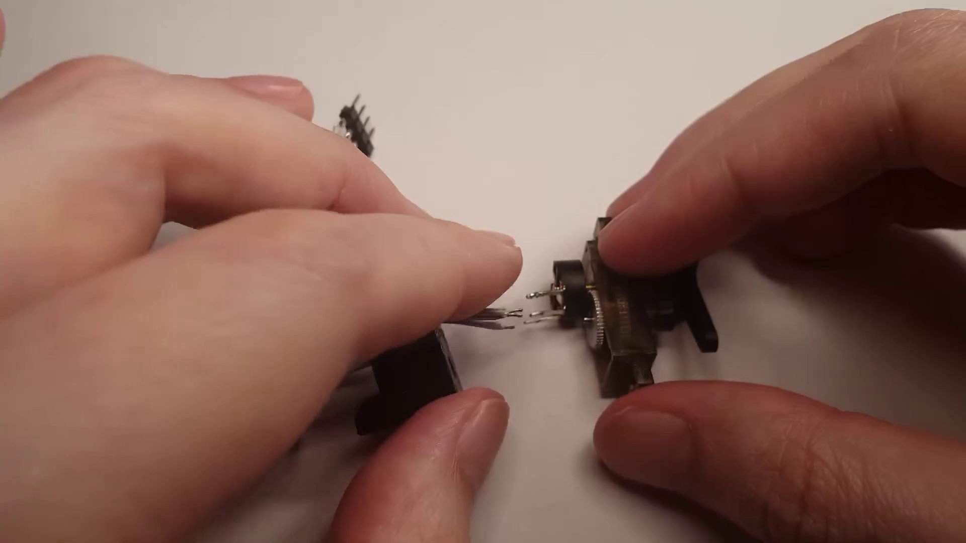
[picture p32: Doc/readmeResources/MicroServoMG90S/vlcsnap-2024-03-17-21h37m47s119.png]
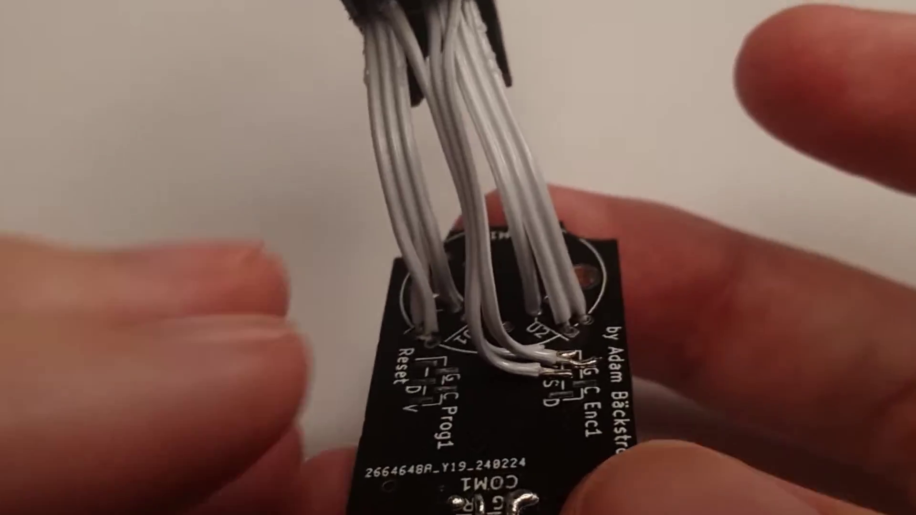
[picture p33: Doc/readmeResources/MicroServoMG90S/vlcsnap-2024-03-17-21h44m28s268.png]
     

7. Put `baseBushing` on the center axis of the gear box

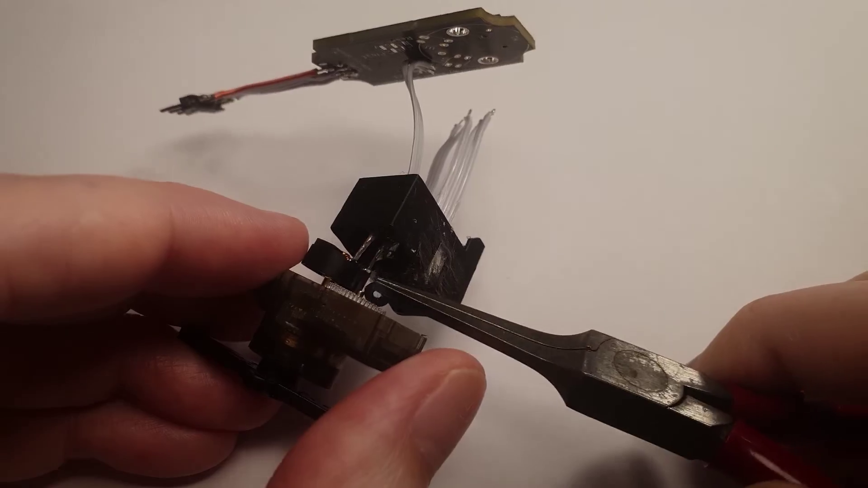
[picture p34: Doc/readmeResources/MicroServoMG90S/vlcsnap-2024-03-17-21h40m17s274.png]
    

8. Insert motor into `baseBox`, solder motor connections to PCB and screw everything together

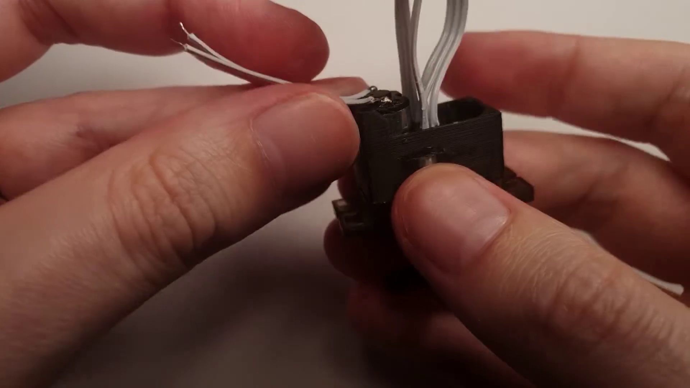
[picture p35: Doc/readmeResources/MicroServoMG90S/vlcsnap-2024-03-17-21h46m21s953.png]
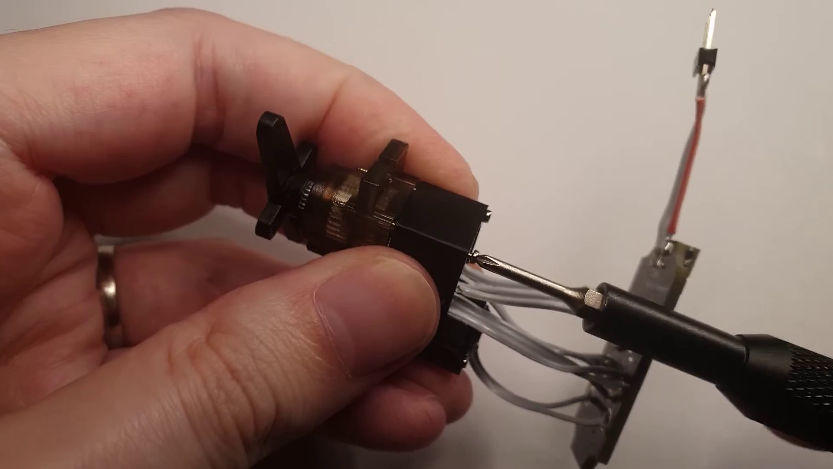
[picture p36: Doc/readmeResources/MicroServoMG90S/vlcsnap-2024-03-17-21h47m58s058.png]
     

9. Done

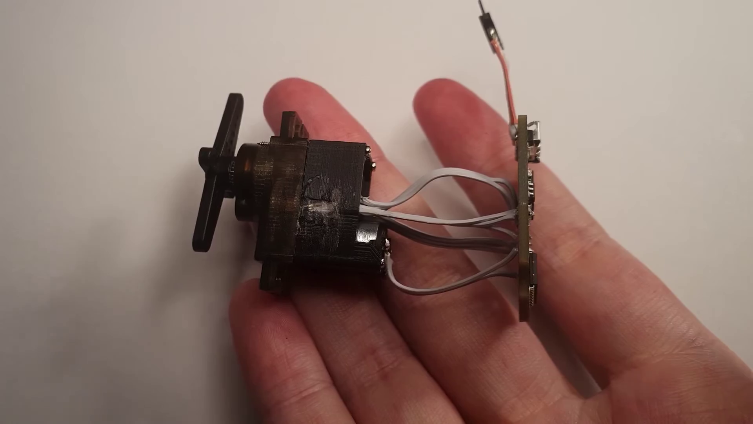
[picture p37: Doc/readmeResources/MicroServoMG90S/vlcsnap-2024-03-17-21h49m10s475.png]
    

### Configure

1. Power servo (5 volt) via pin header and connect to computer via micro USB

2. Run `python3 ./ArduinoSketch/configurationWizard.py`

3. Create a new configuration file by clicking `Create new`, select `defaultMG90S.h` as template, and choose communication node nr

4. Transfer the initial configuration to the servo by clicking `Transfer to target`

5. Select `Optical Encoder` to calibrate encoder

    Calibration example:
    1. Move servo to 100 deg and Lock position by clicking `Lock`
    2. Set `Motor pwm value` to 320
    3. Set `Start motor pwm value` to 450
    4. Choose position resolution `Fine (~4 min)` or `Ultra (~8 min)`
    5. Click `Start calibration`

6. Identify system parameters with `Pwm and system identification`

    Calibration example:
    1. Move servo to 100 deg and Lock position by clicking `Lock`
    2. Set `Motor settle time` to 0.1 s
    3. Set `Min motor pwm value` to 320
    4. Set `Max motor pwm value` to 1023
    5. Set `System model cycle time` to 0.6 ms
    6. Click `Start calibration`

7. Calibrate motor position dependent disturbances with `Motor cogging torque` (optional)

    Calibration example:
    1. Click `Set advanced parameters`
    2. Set `Control speed` to 32
    3. Set `Inertia margin` to 2.0
    4. Click `OK`
    5. Set position resolution to `Standard (~3 min)`
    6. Move servo to 100 deg
    7. Click `Start calibration`

8. Calibrate nonlinearities in output potentiometer with `Output encoder calibration` (optional)

    Calibration example:
    1. Click `Set advanced parameters`
    2. Set `Control speed` to 28
    3. Set `Inertia margin` to 1.8
    4. Click `OK`
    5. Set position resolution to `Fine (~4 min)`
    6. Move servo to 100 deg
    7. Click `Start calibration`

9. To test the final configuration select `Test control loop`

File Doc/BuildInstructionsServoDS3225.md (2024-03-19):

## Part list

* DS3225 MG servo
* 2 x ITR8307
* Custom PCB
* Flat cables
    * 2 leads wide
    * 3 x 3 leads wide
    * 4 leads wide
* pin header 1x4
* 3D printed parts
    * encDisc
    * encDiscTurningMount
    * gearLidBottom
    * gearLidTop
    * optSensorHolder
    * pcbMount

## Build instructions

### Prepare parts

1. Order PCB using gerber, BOM and CPL files:
    - `PcbDesignes/combined/manufacture/gerber.zip`
    - `PcbDesignes/combined/manufacture/jlcpcbPcbaBOM.csv`
    - `PcbDesignes/combined/manufacture/jlcpcbPcbaCPL.csv`

2. Burn bootloader to PCB with a Raspberry Pi

    Power PCB via USB from pi and connect:
    ```
        Prog1:D (swdio) -> GPIO 25
        Prog1:C (swclk) -> GPIO 11
        Prog1:Reset     -> 3.3v

        (GPIO nr are for a Raspberry Pi 3 B)
    ```

     1. Install OpenOCD on the pi with this guide:
           https://learn.adafruit.com/programming-microcontrollers-using-openocd-on-raspberry-pi/compiling-openocd
        
        or using apt-get:
        ```
           sudo apt-get install openocd
        ```
    
     2. Download bootloader:
           https://github.com/adafruit/uf2-samdx1/releases/download/v3.13.0/bootloader-itsybitsy_m0-v3.13.0.bin
    
        or latest from:
           https://github.com/adafruit/uf2-samdx1/releases
          
     3. Put \*.bin file in new folder on pi together with the file [burnBootloaderWithOpenOCD.txt](../PcbDesignes/burnBootloaderWithOpenOCD.txt) and rename the script file to `openocd.cfg`

     4. run:
        ```
           cd \\|Insert name of folder on pi with the script
           sudo openocd
        ```

3. Print objects in PrusaSlicer project file `CadFiles/ServoDS3225/prusaSlicer.3mf`
    
    Print in black PLA:
    - `gearLidBottom.stl`
    - `gearLidTop.stl`
    - `optSensorHolder.stl`
    - `pcbMount.stl`

    Print in white PLA:
    - `encDisc.stl`
    - `encDiscTurningMount.stl`

### Modify the servo

Modify the servo according to the [Build Video](https://youtu.be/Ctb4s6fqnqo?t=21)

Build Video (https://youtu.be/Ctb4s6fqnqo?t=21)

Build steps in video:

1. Disassemble the servo

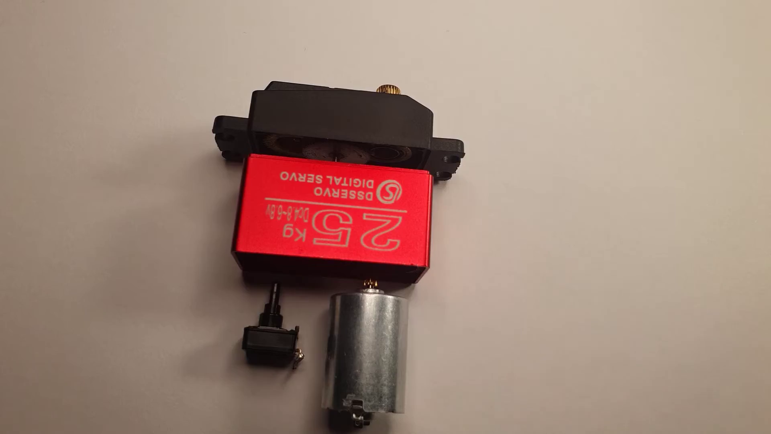
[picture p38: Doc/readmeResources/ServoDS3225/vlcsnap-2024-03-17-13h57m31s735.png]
    

2. The `encDisc` part has to  be completely smooth and free from defects. Getting the required resolution out of a normal FDM 3D printer is basically impossible. So to get a smooth `encDisc` part we first need to file it down while spinning it:

    1. Remove the gear from the motor and mount `encDiscTurningMount` on motor axis. Then mount `encDisc` on `encDiscTurningMount`

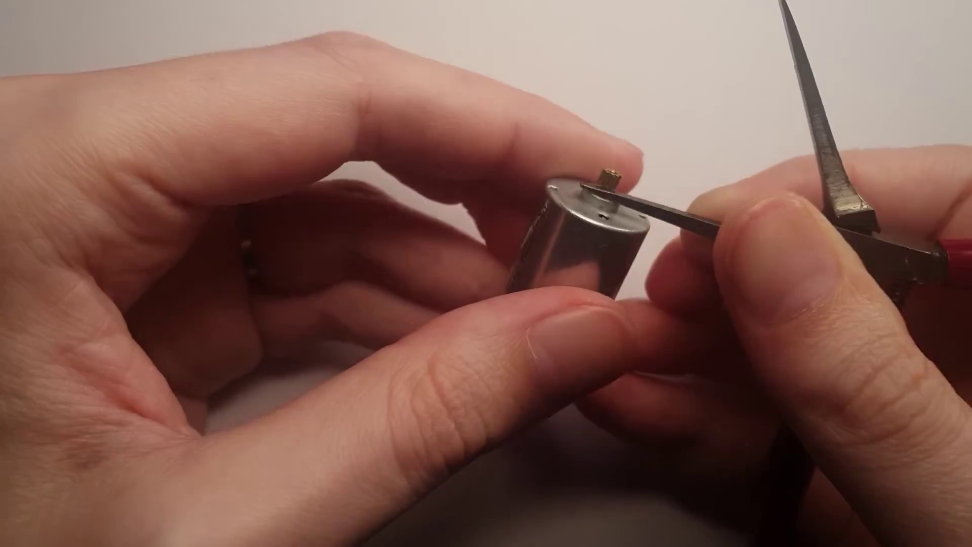
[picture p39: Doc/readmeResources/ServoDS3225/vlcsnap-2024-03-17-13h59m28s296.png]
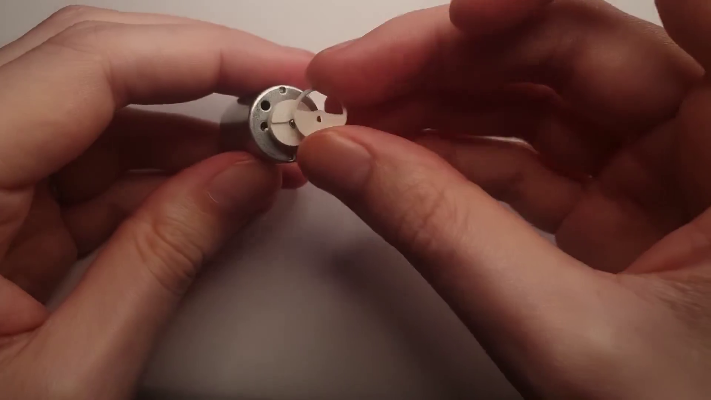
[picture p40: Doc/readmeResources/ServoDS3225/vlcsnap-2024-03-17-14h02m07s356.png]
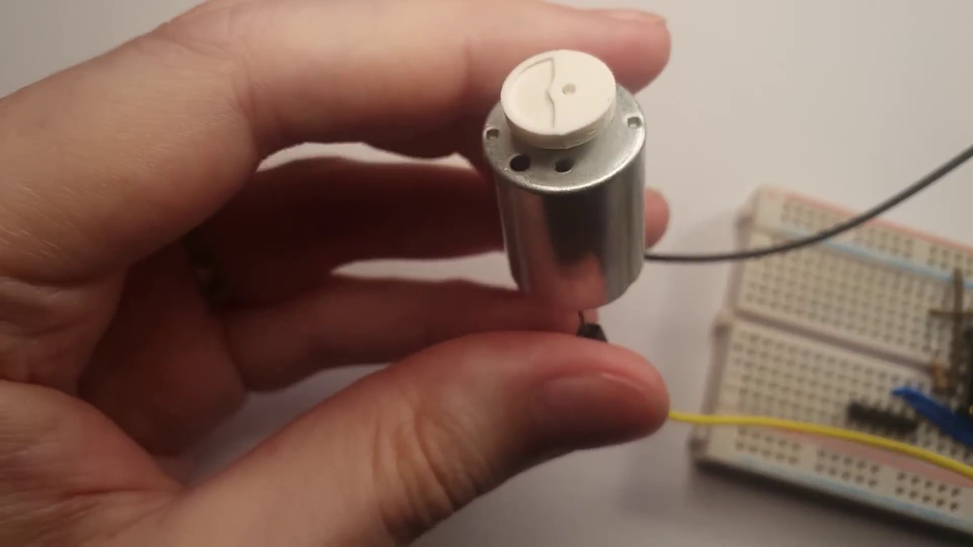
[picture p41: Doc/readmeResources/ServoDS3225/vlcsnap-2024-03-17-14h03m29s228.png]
          

    2. Apply 3-5 volts to the motor and file down 3D printing seams and printing lines until the surface of `encDisc` is completely smooth

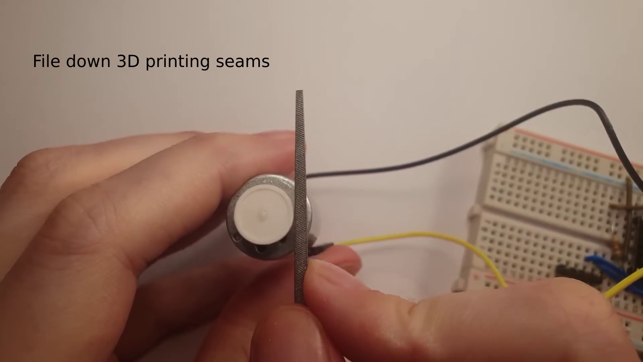
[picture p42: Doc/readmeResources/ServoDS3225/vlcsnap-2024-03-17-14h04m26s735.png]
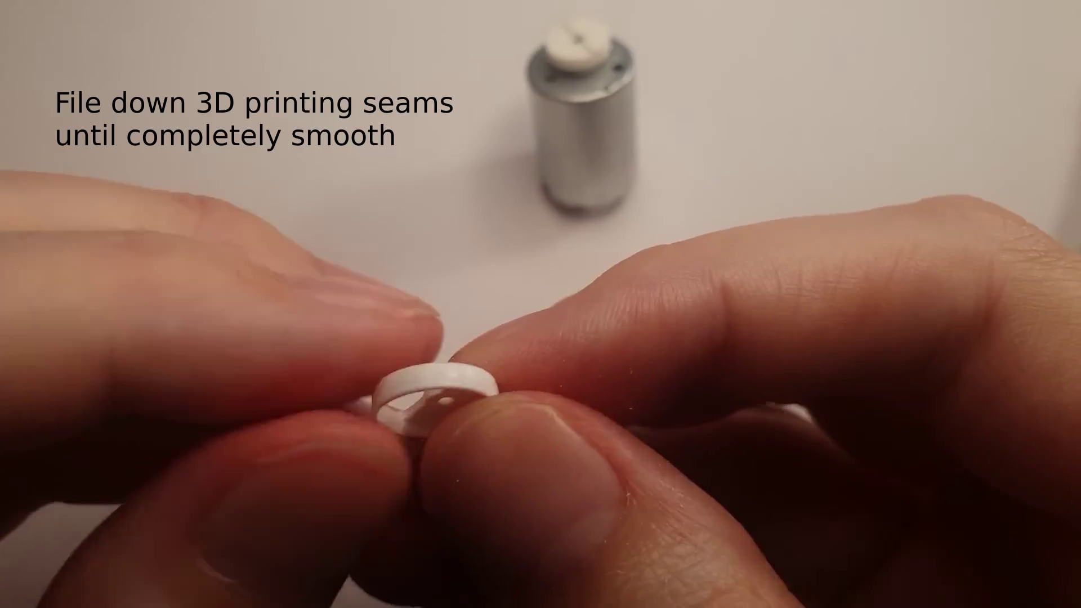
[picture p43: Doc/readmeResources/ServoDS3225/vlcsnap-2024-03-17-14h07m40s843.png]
         

3. Mount the smooth `encDisc` and gear on the motor axis. Then glue `optSensorHolder` to the motor

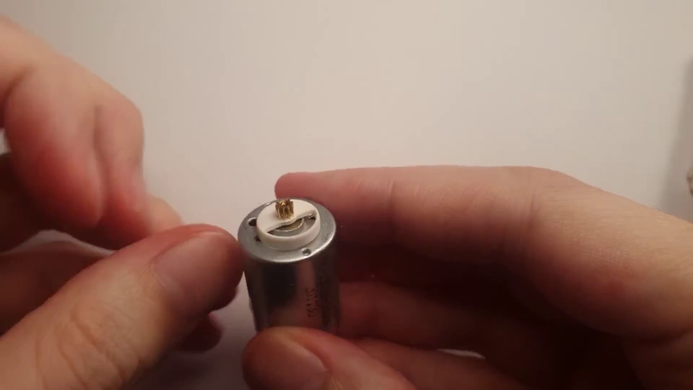
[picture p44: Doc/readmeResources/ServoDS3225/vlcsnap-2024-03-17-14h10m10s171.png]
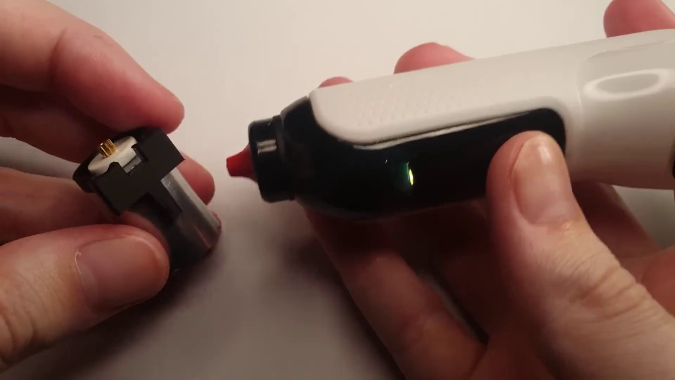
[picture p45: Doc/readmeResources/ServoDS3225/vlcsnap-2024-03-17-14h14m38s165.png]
     

4. Solder on a 3 lead wide flat cable to each of the two ITR8307 sensors. Make sure that the orientation of the sensors are mirrored

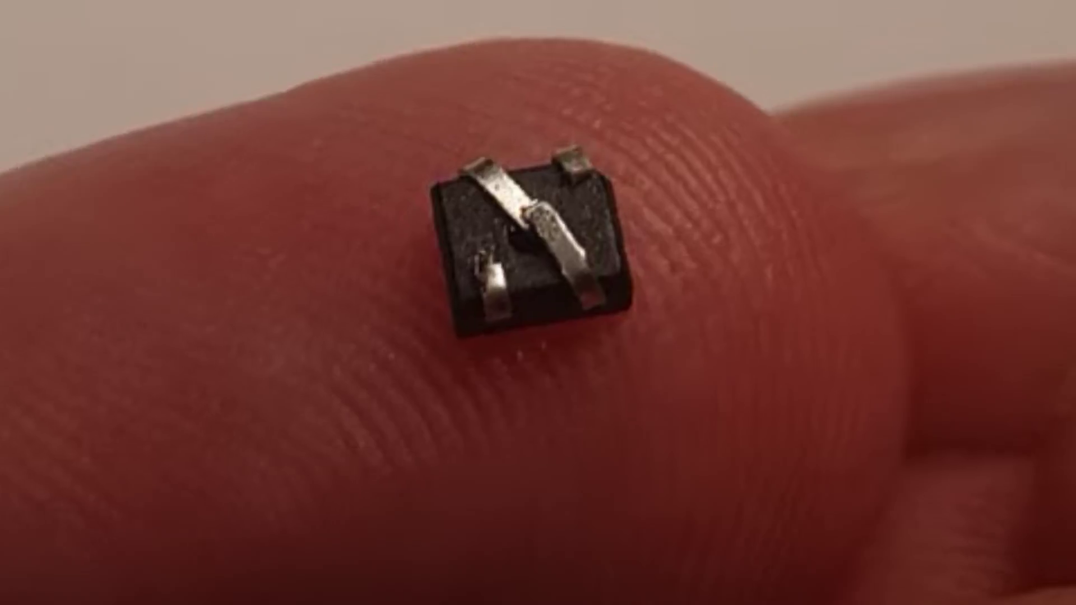
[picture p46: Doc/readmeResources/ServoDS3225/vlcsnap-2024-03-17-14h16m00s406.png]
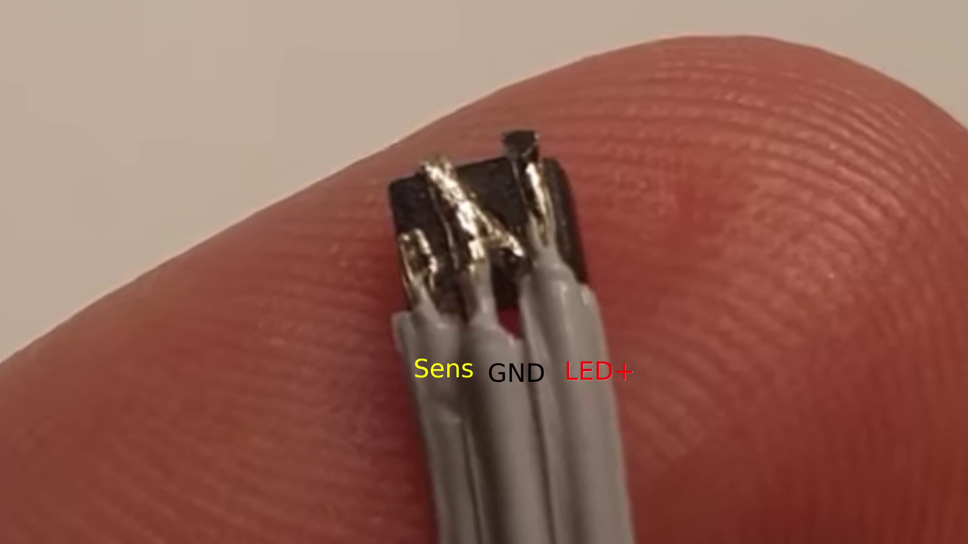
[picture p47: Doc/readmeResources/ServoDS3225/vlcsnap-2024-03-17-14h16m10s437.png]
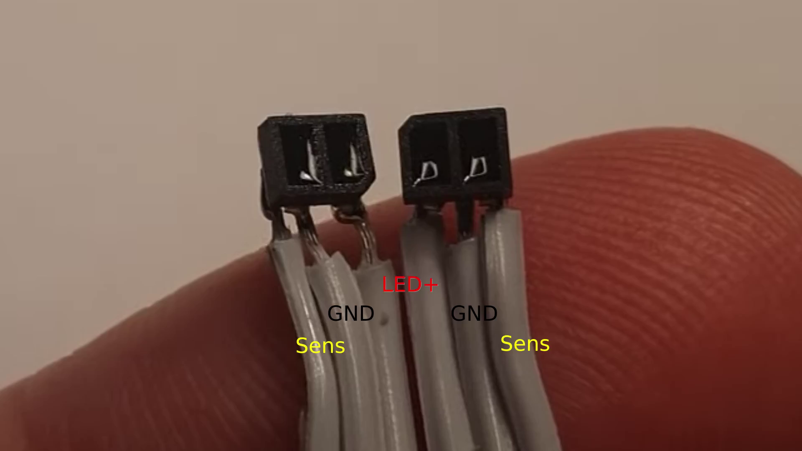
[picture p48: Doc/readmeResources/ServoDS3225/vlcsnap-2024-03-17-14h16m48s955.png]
      

5. Mount the sensors in `optSensorHolder` so that the LED segment (pin 1) of the sensor are oriented towards each other

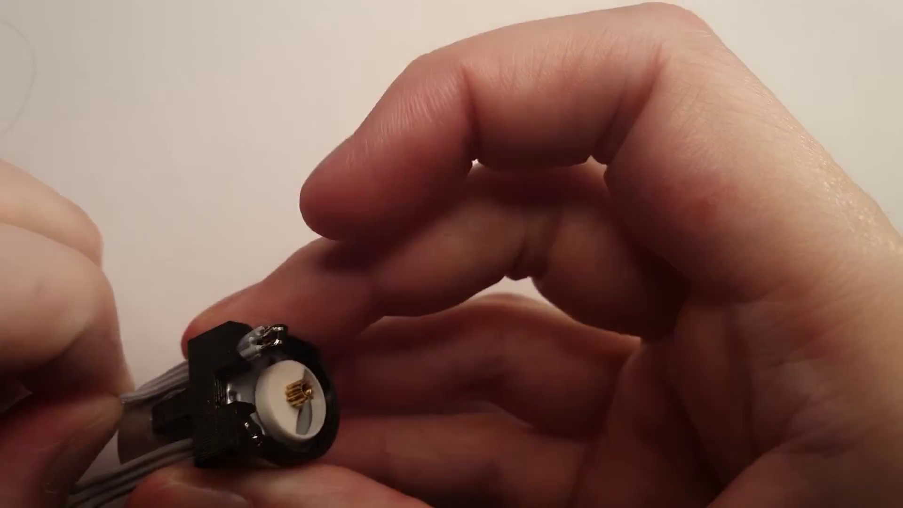
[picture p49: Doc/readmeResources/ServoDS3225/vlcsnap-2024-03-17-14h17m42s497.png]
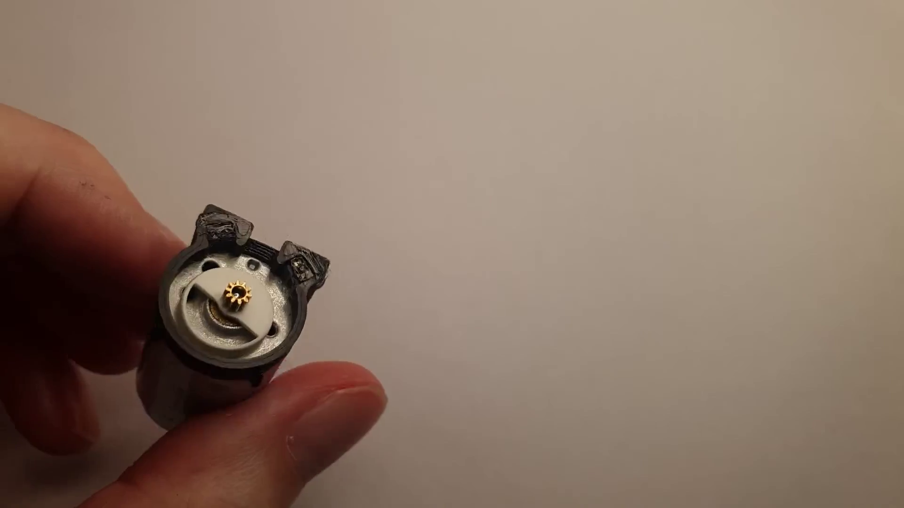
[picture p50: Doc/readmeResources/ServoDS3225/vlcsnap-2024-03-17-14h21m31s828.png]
     

6. Solder the ITR8307 sensors and potentiometer to the PCB

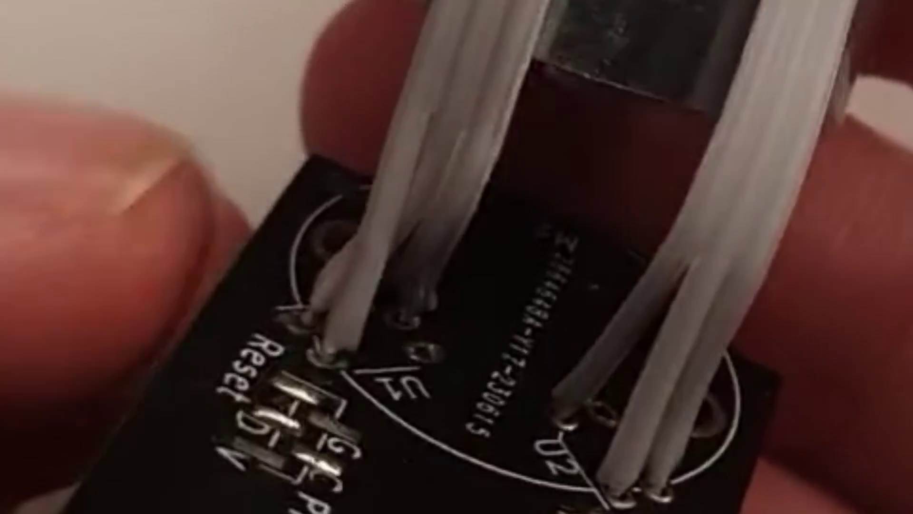
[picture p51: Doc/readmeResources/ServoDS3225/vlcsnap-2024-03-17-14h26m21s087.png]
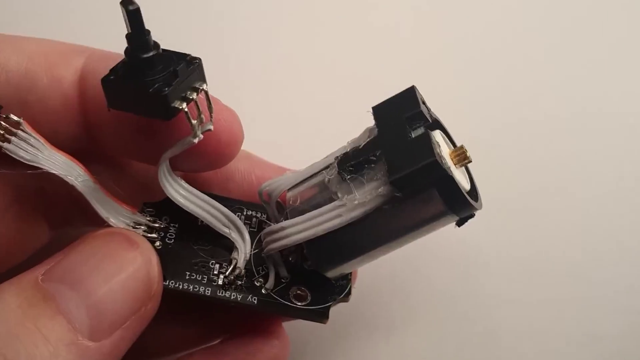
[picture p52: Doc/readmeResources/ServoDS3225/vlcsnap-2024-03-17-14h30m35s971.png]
     

7. Mount `gearLidTop` to the gear box

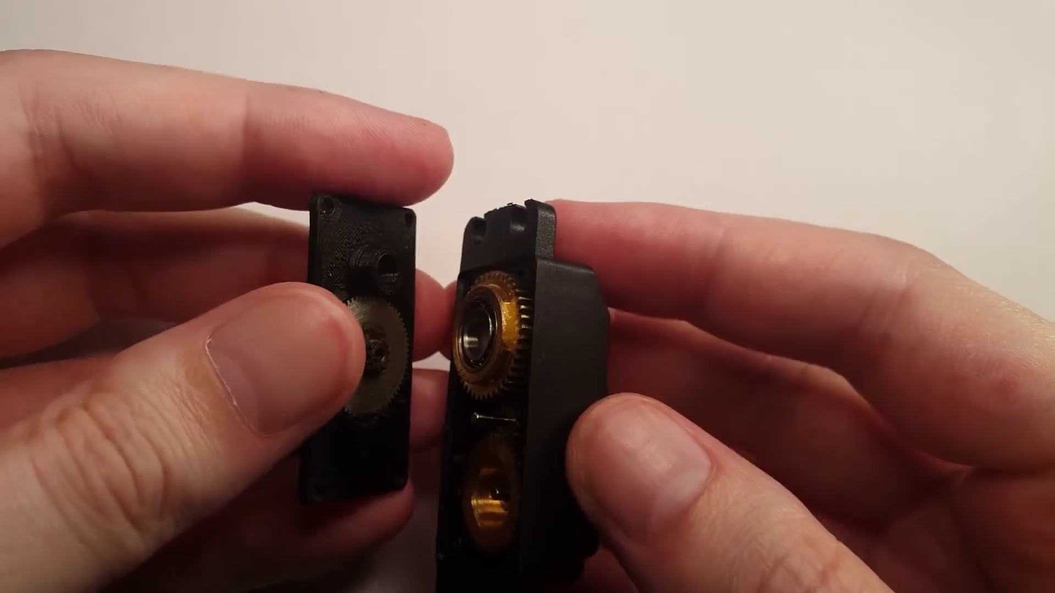
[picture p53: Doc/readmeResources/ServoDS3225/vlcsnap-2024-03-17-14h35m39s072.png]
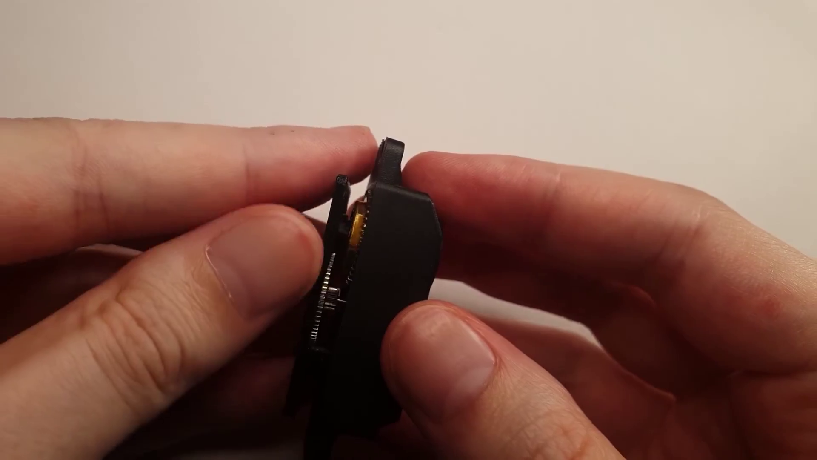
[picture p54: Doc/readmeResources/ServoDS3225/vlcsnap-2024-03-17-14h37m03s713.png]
     

8. Mount `gearLidBottom`, `optSensorHolder` and the potentiometer together with the aluminum heat sink

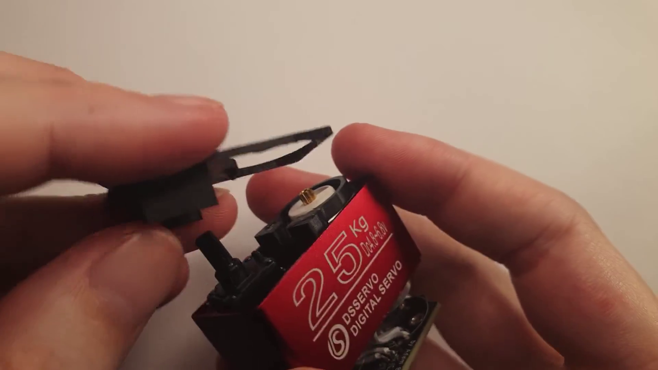
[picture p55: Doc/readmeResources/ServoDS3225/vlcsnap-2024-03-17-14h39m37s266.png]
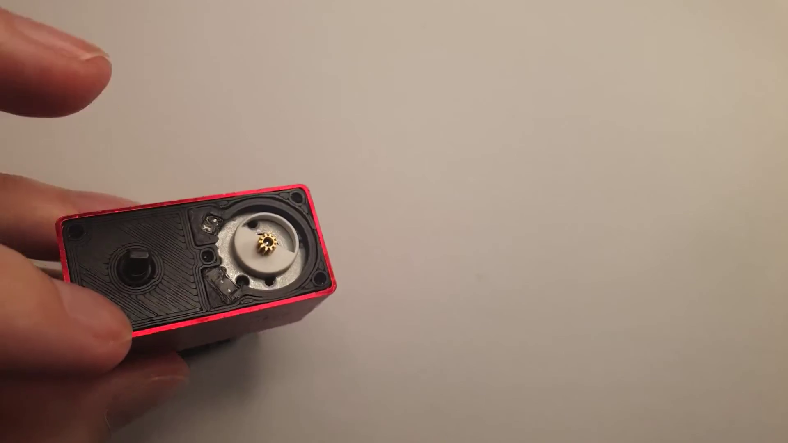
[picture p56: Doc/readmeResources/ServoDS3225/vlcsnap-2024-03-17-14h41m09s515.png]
     

90. Mount `pcbMount` and screw everything together

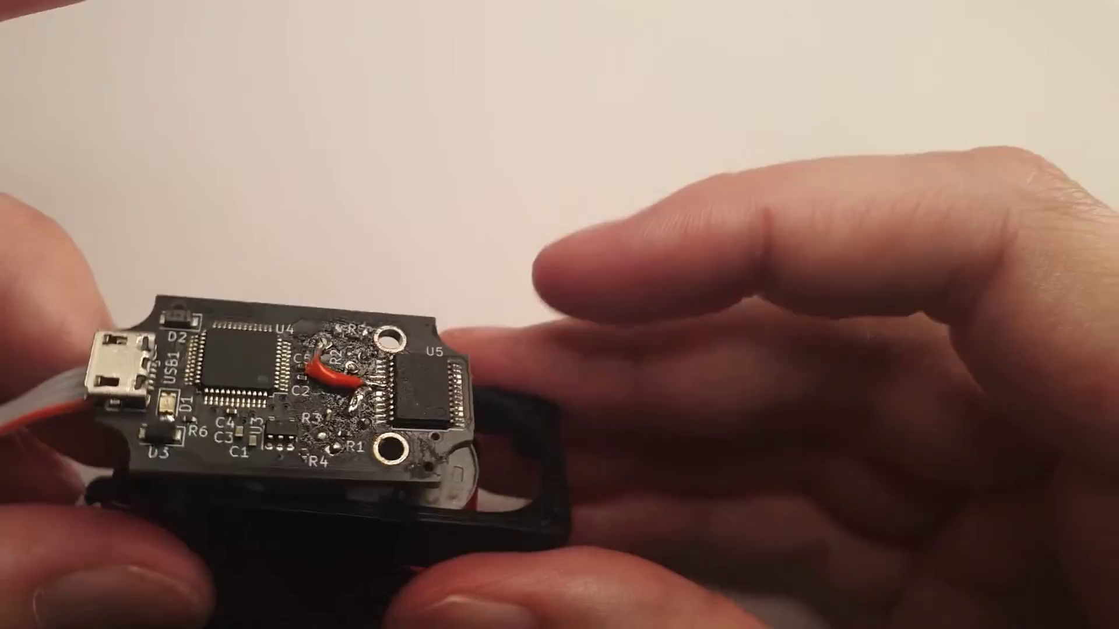
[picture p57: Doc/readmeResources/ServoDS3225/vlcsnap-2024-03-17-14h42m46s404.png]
     

10. Glue the PCB to the `pcbMount` and solder the motor connections

     

### Configure

1. Power servo (5 volt) via pin header and connect to computer via micro USB

2. Run `python3 ./ArduinoSketch/configurationWizard.py`

3. Create a new configuration file by clicking `Create new`, select `defaultDS3225.h` as template, and choose communication node nr

4. Transfer the initial configuration to the servo by clicking `Transfer to target`

5. Select `Optical Encoder` to calibrate encoder

    Calibration example:
    1. Move servo to 110 deg and Lock position by clicking `Lock`
    2. Set `Motor pwm value` to 610
    3. Set `Start motor pwm value` to 650
    4. Choose position resolution `Fine (~4 min)` or `Ultra (~8 min)`
    5. Click `Start calibration`

6. Identify system parameters with `Pwm and system identification`

    Calibration example:
    1. Move servo to 110 deg and Lock position by clicking `Lock`
    2. Set `Motor settle time` to 0.1 s
    3. Set `Min motor pwm value` to 590
    4. Set `Max motor pwm value` to 1023
    5. Set `System model cycle time` to 0.6 ms
    6. Click `Start calibration`

7. Calibrate motor position dependent disturbances with `Motor cogging torque`

    Calibration example:
    1. Click `Set advanced parameters`
    2. Set `Control speed` to 32
    3. Set `Inertia margin` to 2.0
    4. Click `OK`
    5. Set position resolution to `Standard (~3 min)`
    6. Move servo to 110 deg
    7. Click `Start calibration`

8. Calibrate nonlinearities in output potentiometer with `Output encoder calibration` (optional)

    Calibration example:
    1. Click `Set advanced parameters`
    2. Set `Control speed` to 28
    3. Set `Inertia margin` to 1.8
    4. Click `OK`
    5. Set position resolution to `Fine (~4 min)`
    6. Move servo to 110 deg
    7. Click `Start calibration`

9. To test the final configuration select `Test control loop`

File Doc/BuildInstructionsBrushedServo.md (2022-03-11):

Brushed servo modification (DS3225 MG)
--------

### Part list

* 1 x DS3225 MG servo
* 1 x Custom PCB
  * PcbDesignes/ServoBrushed/combined/manufacture
* 2 x ITR8307

Cad and stl files for 3D printing:
```
CadFiles/ServoBrushed
```

Electrical schematic:
```
PcbDesignes/ServoBrushed
```

### Build instructions

[](https://youtu.be/ECLrLupFW10?t=94)
[Video Tutorial](https://youtu.be/ECLrLupFW10?t=94)

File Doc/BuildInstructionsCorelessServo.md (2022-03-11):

Coreless servo modification (Turnigy MG959)
--------

### Part list

* 1 x Turnigy MG959 servo
* 1 x Adafruit ItsyBitsy M0 Express
  * https://learn.adafruit.com/introducing-itsy-bitsy-m0
* 1 x SparkFun Motor Driver - Dual TB6612FNG (1A)
  * https://www.sparkfun.com/products/14451
* 1 x as5048A + 6mm x 2mm comopatible magnet
  * https://ams.com/as5048a
* 2 x ITR8307
* 2 x 8.2 kohm resistor
* 2 x 120 ohm resistor

Cad and stl files for 3D printing:
```
CadFiles/ServoCoreless
```

Electrical schematic:
```
PcbDesignes/ServoCoreless
```
### Build instructions

#### Build MainPcb and AS5048aEncoderBoard

A video on how to build the MainPcb and AS5048aEncoderBoard can be found at https://youtu.be/YQpAAr5RPSE?t=60.
This video is for an older version but the building instructions are the same.

#### Servo gearbox with 3D printed parts

|  | 
| --- |

#### PCB Assemblies

|  | 
| --- |

#### How to mount the PCBs to servo

|  |  |
| --- | --- |

|  |  |
| --- | --- |

#### Build the Optical Encoder

|  |  |  |
| --- | --- | --- |

1) Take the motor, use pliers to bend out the four indents in the metal housing and bend up the motor lid.

|  |  |  |
| --- | --- | --- |

2) Remove the two steel brushes from the lid carefully by cutting the lid into pieces. Take the 3D printed motor lid and insert the two steel brushes and two ITR8307 into the new lid. Solder the ITR8307 according to:
```
PcbDesignes/Servo/OpticalEncoder/OpticalEncoder.sch
```

|  |  |  |
| --- | --- | --- |

3) Take the motor with the lid removed. Paint the rotor with black nail polish and glue in the optical encoder wheel on top as shown in the middle image. The dimensions of the encoder wheel can be found in:
```
CadFiles/Servo/OpticalEncoderWheelDimensions.png

```
Then carefully put the new lid on the motor without bending the steel brushes.

|  | 
| --- |

4) Solder the four leads from the optical encoder on top of ItsyBitsy board as shown in this image.

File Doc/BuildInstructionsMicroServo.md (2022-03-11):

Micro servo modification (MG90S or SG90)
--------

### Part list

* 1 x MG90S servo
* 1 x Adafruit ItsyBitsy M0 Express
  * https://learn.adafruit.com/introducing-itsy-bitsy-m0
* 1 x SparkFun Motor Driver - Dual TB6612FNG (1A)
  * https://www.sparkfun.com/products/14451
* 2 x ITR8307
* 2 x 120 ohm resistor
* 1 x 6.8 kohm resistor
* 1 x 1.5 kohm resistor

Cad and stl files for 3D printing:
```
CadFiles/MicroServo
```

Electrical schematic:
```
PcbDesignes/MicroServo
```

### Build instructions

|  |  |  |
| :-- | :-- | :-- |

1) Open the servo, desolder the motor and the potentiometer

|  |  |  |
| --- | --- | --- |

2) Bend down the motor terminals and remove the plastic back axis cover so the motor looks like the one in the last image

|  |  |  |
| --- | --- | --- |

3) Place one of the holes on a servo horn over the axis. Then use a screw and a vice to push out the motor axis about 1 mm so it looks like the motor in the last image.

|  |  |  |
| --- | --- | --- |

4) Then solder two wires to the motor terminals. Use super glue to mount the optical encoder wheel to the back axis and mount the 3D printed "OpticalEncoderSensorMount" part over the back of the motor.

|  |  |  |
| --- | --- | --- |

5) Place the two IR sensors next to each other on a piece of tape and put some hot glue over them. Fold pin 4 of the lower sensor like the middle picture shows. Then fold in the rest of the ground pins, cut them to length and solder them together.

|  |  |  |
| --- | --- | --- |

6) Place the four resistors next to each other on a piece of tape, in the order 6.8k, 120, 1.5k and 120 ohm from right to left. Put some hot glue over them to hold them together and remove the tape. Fold the top leg of the 6.8k resistor like the middle picture shows. Then fold in the rest of the 3.3V pins and solder them together.

|  |  |
| --- | --- |

7) Connect the two 120 ohm resistors to pin 1 on the IR sensors and the 6.8k and 1.5k ohm resistors to pin 3.

|  |
| --- |

8) Solder three wires to the potentiometer.

|  |  |  |
| --- | --- | --- |

9) Connect the potentiometers 3.3V and ground to the optical encoder sensors while soldering on a 5 wire flat cable to the assembly. Then connect the third wire of the flat cable to the potentiometer sens wire and connect the fourth and fifth wires to the IR sensors third pin. This wires up the flat cable so that from right to left we have: 3.3V, GND, output shaft potentiometer, optical encoder channel A and lastly channel B.

|  |  |  |
| --- | --- | --- |

10) Glue the optical encoder sensors to the "OpticalEncoderSensorMount". Cut the screws to a length so that they fit with the servo lid removed.

|  |
| --- |

11) Put back the motor and the potentiometer into the servo. See "PcbDesignes/MicroServo/MainPcb/MainPcb.sch" for info on how to connect the microcontroller and motor driver.

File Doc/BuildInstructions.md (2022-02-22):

# Build instructions

Hardware
--------

### Parts list

#### Modified coreless servo
* 1 x Turnigy MG959 servo
* 1 x Adafruit ItsyBitsy M0 Express
  * https://learn.adafruit.com/introducing-itsy-bitsy-m0
* 1 x SparkFun Motor Driver - Dual TB6612FNG (1A)
  * https://www.sparkfun.com/products/14451
* 1 x as5048A + 6mm x 2mm comopatible magnet
  * https://ams.com/as5048a
* 2 x ITR8307
* 2 x 8.2 kohm resistor
* 2 x 120 ohm resistor

Cad and stl files for 3D printing:
```
CadFiles/ServoCoreless
```

Electrical schematic:
```
PcbDesignes/ServoCoreless
```

#### Modified micro servo
* 1 x MG90S servo
* 1 x Adafruit ItsyBitsy M0 Express
  * https://learn.adafruit.com/introducing-itsy-bitsy-m0
* 1 x SparkFun Motor Driver - Dual TB6612FNG (1A)
  * https://www.sparkfun.com/products/14451
* 2 x ITR8307
* 2 x 120 ohm resistor
* 1 x 6.8 kohm resistor
* 1 x 1.5 kohm resistor

Cad and stl files for 3D printing:
```
CadFiles/MicroServo
```

Electrical schematic:
```
PcbDesignes/MicroServo
```

#### Gripper
* 1 x SG90 servo

".stl" files for 3D printing:
```
CadFiles/Robot/stl/GripperBase.stl
CadFiles/Robot/stl/GripperClip.stl
CadFiles/Robot/stl/GripperFinger1.stl
CadFiles/Robot/stl/GripperFinger2.stl
CadFiles/Robot/stl/GripperMount.stl
```

#### Robot
* 3 x Modified coreless servo
* 3 x Modified micro servo
* 1 x Gripper
* 1 x 10 x 10 mm square aluminum bar (about 500 mm)
* 1 x 15 x 15 mm square aluminum bar (about 100 mm)
* 1 x 5V Powersuply 
* 1 x Fast USB to serial microcontroller (Adafruit ItsyBitsy M0 Express or Arduino MKR Zero)
  * https://learn.adafruit.com/introducing-itsy-bitsy-m0
  * https://store.arduino.cc/arduino-mkr-zero-i2s-bus-sd-for-sound-music-digital-audio-data

Cad and stl files for 3D printing:
```
CadFiles/Robot
```

## Coreless servo modification (Turnigy MG959)

#### Build MainPcb and AS5048aEncoderBoard

A video on how to build the MainPcb and AS5048aEncoderBoard can be found at https://youtu.be/YQpAAr5RPSE?t=60.
This video is for an older version but the building instructions are the same.

#### Servo gearbox with 3D printed parts

|  | 
| --- |

#### PCB Assemblies

|  | 
| --- |

#### How to mount the PCBs to servo

|  |  |
| --- | --- |

|  |  |
| --- | --- |

#### Build the Optical Encoder

|  |  |  |
| --- | --- | --- |

1) Take the motor, use pliers to bend out the four indents in the metal housing and bend up the motor lid.

|  |  |  |
| --- | --- | --- |

2) Remove the two steel brushes from the lid carefully by cutting the lid into pieces. Take the 3D printed motor lid and insert the two steel brushes and two ITR8307 into the new lid. Solder the ITR8307 according to:
```
PcbDesignes/Servo/OpticalEncoder/OpticalEncoder.sch
```

|  |  |  |
| --- | --- | --- |

3) Take the motor with the lid removed. Paint the rotor with black nail polish and glue in the optical encoder wheel on top as shown in the middle image. The dimensions of the encoder wheel can be found in:
```
CadFiles/Servo/OpticalEncoderWheelDimensions.png

```
Then carefully put the new lid on the motor without bending the steel brushes.

|  | 
| --- |

4) Solder the four leads from the optical encoder on top of ItsyBitsy board as shown in this image.

## Micro servo modification (MG90S or SG90)

|  |  |  |
| :-- | :-- | :-- |

1) Open the servo, desolder the motor and the potentiometer

|  |  |  |
| --- | --- | --- |

2) Bend down the motor terminals and remove the plastic back axis cover so the motor looks like the one in the last image

|  |  |  |
| --- | --- | --- |

3) Place one of the holes on a servo horn over the axis. Then use a screw and a vice to push out the motor axis about 1 mm so it looks like the motor in the last image.

|  |  |  |
| --- | --- | --- |

4) Then solder two wires to the motor terminals. Use super glue to mount the optical encoder wheel to the back axis and mount the 3D printed "OpticalEncoderSensorMount" part over the back of the motor.

|  |  |  |
| --- | --- | --- |

5) Place the two IR sensors next to each other on a piece of tape and put some hot glue over them. Fold pin 4 of the lower sensor like the middle picture shows. Then fold in the rest of the ground pins, cut them to length and solder them together.

|  |  |  |
| --- | --- | --- |

6) Place the four resistors next to each other on a piece of tape, in the order 6.8k, 120, 1.5k and 120 ohm from right to left. Put some hot glue over them to hold them together and remove the tape. Fold the top leg of the 6.8k resistor like the middle picture shows. Then fold in the rest of the 3.3V pins and solder them together.

|  |  |
| --- | --- |

7) Connect the two 120 ohm resistors to pin 1 on the IR sensors and the 6.8k and 1.5k ohm resistors to pin 3.

|  |
| --- |

8) Solder three wires to the potentiometer.

|  |  |  |
| --- | --- | --- |

9) Connect the potentiometers 3.3V and ground to the optical encoder sensors while soldering on a 5 wire flat cable to the assembly. Then connect the third wire of the flat cable to the potentiometer sens wire and connect the fourth and fifth wires to the IR sensors third pin. This wires up the flat cable so that from right to left we have: 3.3V, GND, output shaft potentiometer, optical encoder channel A and lastly channel B.

|  |  |  |
| --- | --- | --- |

10) Glue the optical encoder sensors to the "OpticalEncoderSensorMount". Cut the screws to a length so that they fit with the servo lid removed.

|  |
| --- |

11) Put back the motor and the potentiometer into the servo. See "PcbDesignes/MicroServo/MainPcb/MainPcb.sch" for info on how to connect the microcontroller and motor driver.

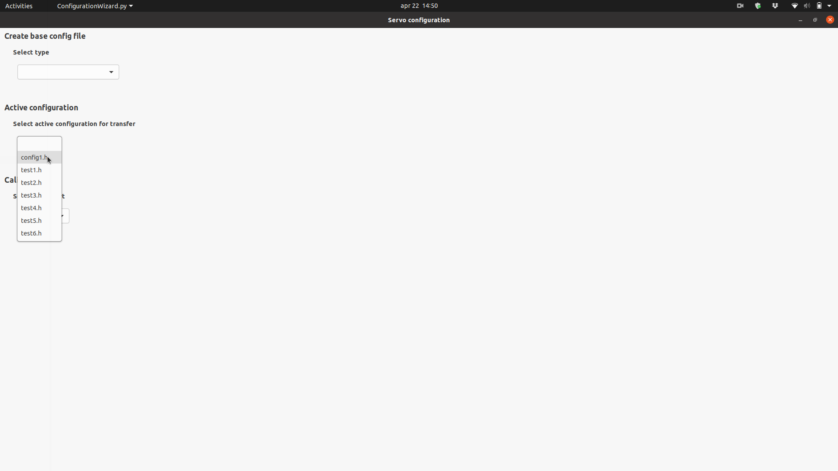
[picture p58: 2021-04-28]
Doc/readmeResources/arduinoSetup/step2.png

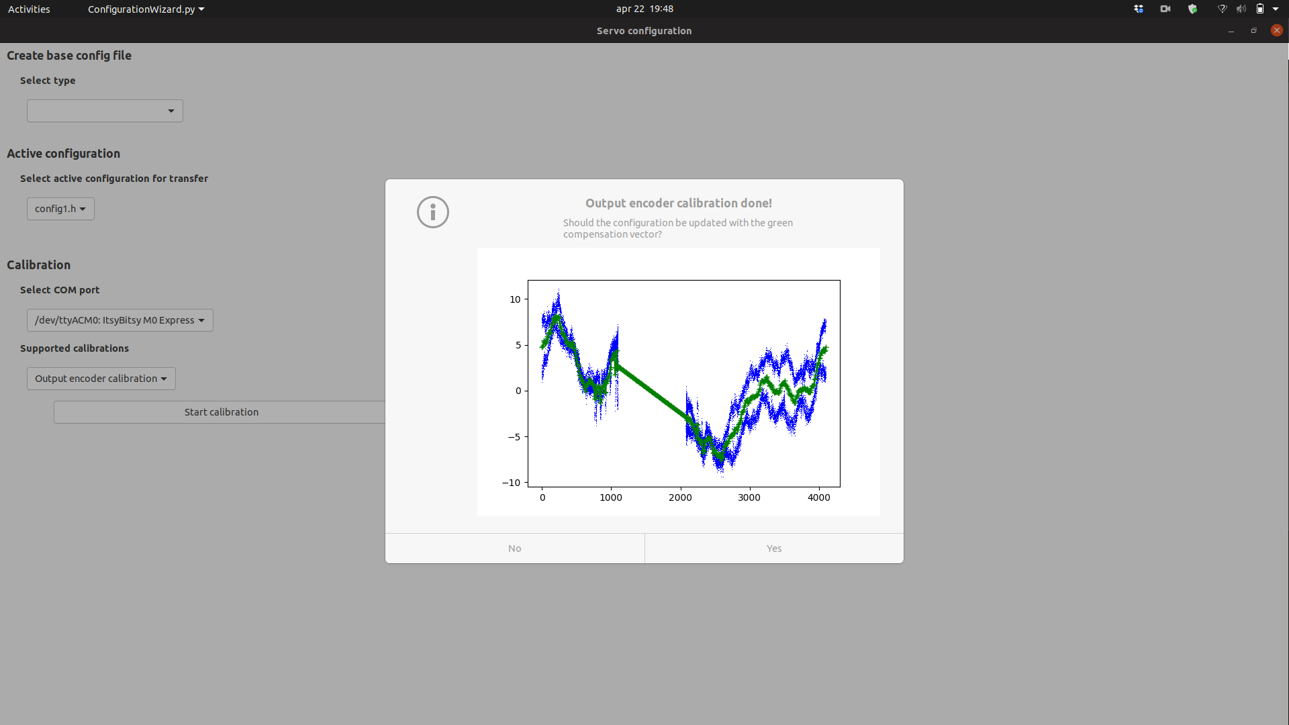
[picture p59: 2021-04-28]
Doc/readmeResources/arduinoSetup/step6.png

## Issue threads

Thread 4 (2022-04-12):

Brushed servos

Telepresent, 2022-04-12:
For building the robot you mention to use 3x coreless modified servos + 3x micro modified servos. Brushed servos are not required? Finding ATSAMD21G18A-A at a reasonable price for a custom PCB is very difficult this days. So, can we build the robot just with off the shelf boards?

adamb314, 2022-04-13:
That is correct, the current robot version does not use the modded DS3225. However, the MG959 can be replaced with DS3225 if someone wants to.

The reason behind the custom PCB is purely for convenience, so you can use Adafruit ItsyBitsy M0 Express boards instead if you want.

vkumarsinghnoida, 2022-04-29:
> That is correct, the current robot version does not use the modded DS3225. However, the MG959 can be replaced with DS3225 if someone wants to.
>
> The reason behind the custom PCB is purely for convenience, so you can use Adafruit ItsyBitsy M0 Express boards instead if you want.

But will the program be the same and can we use any other board ?

Closed 2022-04-18.

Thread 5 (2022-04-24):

No current sensor？

pzh11001, 2022-04-24:
What a great project！
I noticed that previous versions had current sensors and corresponding control codes。
However, in the latest version, there is no current sensor on the circuit diagram. However, there is still a current sampling part in the code. Is that right?

adamb314, 2022-04-24:
Thank you!

Yes that is correct. In the latest version I replaced the current controller with a sensorless model based approach, the CurrentControlModel class. Mainly to simplify the design but also because of the high noise levels of the current sensor. However, I left the old CurrentControlLoop class implementation if someone wants to change back to it for their design.

pzh11001, 2022-04-25:
>
I'm sorry I didn't read it carefully enough
Oh, yes. I noticed that. Although there is code for  CurrentControlLoop, the program logic is not actually called. This program is called CurrentControlModel。
According to my analysis of the code principle, the whole code actually has only three threads running independently: a main thread, a Controlloop thread of DCservo class, and a Statuslighthandler thread. The main servo control logic is executed in the Controlloop thread. However, since this is an ISR calling method based on timer interrupt, won't the execution of so much code in the interrupt function cause the CPU to get stuck？ because as far as I know, there should be very simple code in the ISR calling method.

adamb314, 2022-04-25:
No worries.

If it was a normal interrupt handler on the SAMD21 CPU you would be correct, but everything is taken care of by the ThreadHandler. If you want more information about it you could check out this: https://books.google.se/books?id=l9RtBgAAQBAJ&pg=PA673. Page 673 show the stack frame hacking I am using in platformSpecificClasses.cpp.

pzh11001, 2022-04-25:
> No worries.
>
> If it was a normal interrupt handler on the SAMD21 CPU you would be correct, but everything is taken care of by the ThreadHandler. If you want more information about it you could check out this: https://books.google.se/books?id=l9RtBgAAQBAJ&pg=PA673. Page 673 show the stack frame hacking I am using in platformSpecificClasses.cpp.

Thank you. It's exciting.
Now I want to use your project to make a small steering gear, and then make a small but high-precision 6axis robot arm.

pzh11001, 2022-04-25:
I consider that if a slight torsion spring is added to the output shaft, the gear backlash will always be eliminated in most cases. Although the backlash compensation algorithm is also needed in some cases, it can not happen too often. Because the compensation gap takes time, too free gap is easy to be frequently disturbed by environmental forces.
This should greatly improve the smoothness of the steering gear movement。
I'm going to test this device after reproducing your project

adamb314, 2022-04-25:
Sounds like a good plan. Good luck!

Closed 2022-04-25.

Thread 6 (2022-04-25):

Accuracy achievable

vkumarsinghnoida, 2022-04-25:
Hi Adam,
An awesome project. I was looking greater accuracy in servos for my automatic turret. Can you please tell me how accurate are the modified servos in degrees ?

adamb314, 2022-04-26:
Thank you.
With the latest version (using the the original potentiometer) I have been able to achieve 0.04 degree accuracy.

vkumarsinghnoida, 2022-04-26:
That's great sir. And can I modify my mg995 servo motor amd achieve the
same accuracy.

On Tue, Apr 26, 2022, 2:39 PM Adam Bäckström ***@***.***>
wrote:

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

adamb314, 2022-04-26:
There are of course no guarantees... but it looks similar to the DS3225 I used so it should be possible. Good luck!

vkumarsinghnoida, 2022-04-26:
So what are the main things that a servo should have to follow your
tutorial. Like does the internal motor has to be the same or the size of
the servo should be the same ?

On Tue, Apr 26, 2022, 6:29 PM Adam Bäckström ***@***.***>
wrote:

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

vkumarsinghnoida, 2022-04-29:
> Thank you. With the latest version (using the the original potentiometer) I have been able to achieve 0.04 degree accuracy.

So if I set the angle value to 90.04° will it be accurate or the value would be 90.04 (+/-) 0.04 ?

adamb314, 2022-04-29:
> I had problems with my servo motor so I opened it to solve the problem but I cannot understand where should I position the servo shaft and the pot shaft cause they both need to fit but I want the servos full range of positions. As you have opened so many servos how can I solve the problem ?
>

I am sorry, but I don't really understand what you mean... Do you mean you want 360° of rotation?

> So if I set the angle value to 90.04° will it be accurate or the value would be 90.04 (+/-) 0.04 ?
>

it would be 90.04 (+/-) 0.04

vkumarsinghnoida, 2022-04-29:
I mean to say after I open the servo how do I position my potentiometer and servo shaft like how much should I turn or just fit them together ?

adamb314, 2022-05-01:
I just rotate the shaft until the keyway lignes up with the potentiometers shaft and then push them together.

vkumarsinghnoida, 2022-05-01:
Ok thank you very much.
Can you address my other question regarding the number of boards and the
code compatibility I have asked in another issue ?

On Sun, May 1, 2022, 9:39 PM Adam Bäckström ***@***.***>
wrote:

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

Closed 2022-05-01.

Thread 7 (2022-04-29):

Alternative boards and code

vkumarsinghnoida, 2022-04-29:
Hi
My questions are regarding how to make the servo without custom pcb as given in coreless servo build.
How many boards are required to control 2 servos?
How exactly do we connect the board and use which software ?
And can we use the original potentiometer instead of the magnetic encoder ?

adamb314, 2022-05-01:
1) One "Adafruit ItsyBitsy M0 Express" board per servo
2) a) If you don't want custom PCBs and use a potentiometer you should follow the Schematics in ServoProject/PcbDesignes/MicroServo/MainPcb/MainPcb.sch
b) The same software
3) Using a potentiometer is the default when creating a new configuration

vkumarsinghnoida, 2022-05-02:
1)How can I find the gear ratio of my servo motor as it is not given in the
datasheet ? For the configuration program.

2)And which software do we need to boot the custom pcb and then do we just
run the python code or we need Arduino ide too ?

3)And how can I control it after I have finished all the steps without your
given gui ? Do I have to connect a usb cable or it needs pwm signal ?

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

adamb314, 2022-05-02:
1) best is to count the gear teeth to calculate it.
2) you program the board with the Arduino sketch.
3) please read "Communication bus setup for demo projects"

vkumarsinghnoida, 2022-05-03:
Thanks
Unfortunately I couldn't find communication bus setup code. Can you tell me
it's exact location (how to give the servo and angle)? And I have to
install sublime text to run the bootloader and other code ? Like what are
the steps from scratch.

On Mon, May 2, 2022, 3:09 PM Adam Bäckström ***@***.***>
wrote:

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

adamb314, 2022-05-03:
You do not need to burn the bootloader if you use an off the shelf board, only when you have the custom PCB. I only use sublime text in the video to show text files and terminal output of the GUI.

Open one of the demos (there are Python, C++ and Arduino versions) to see how you control the servos.

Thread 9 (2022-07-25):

Compatibility with DS3218 servos

PJfixer, 2022-07-25:
Hi adam,

First congratulations for your work, your results with theses cheap servos are really impressive

i'm verry interested in building five of them but before checkout on JLCPB, i would like to have your opinion about the PCB compatibility with DS3218 servos.

i think its ok because the only difference with 3225 servos seems to be height , and obviously the final torque.

what do you think ?

Regards,

adamb314, 2022-07-25:
Hi PJfixer, and thank you.
I agree with you, a DS3218 should work too. You might have to modify the height of the back cover though. Good luck with your servo modifications!

PJfixer, 2022-07-26:
great ! thank you ! 👍

Closed 2022-07-26.

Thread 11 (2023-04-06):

Further explanatory materials anywhere?

TTD1024, 2023-04-06:
Excuse me, this is an absolutely excellent project, but while the documentation is great for using the completed system as you have produced it (great work), it doesn't give a detailed description of th underlying theory. Might you be able to provide some links to where you learnt the excellent PID and control techniques* you've employed here, or otherwise some further description of how the double-encoder feedback loop works (more detailed than the diagram presently shown for comparison to classical hobby servo control loops, but more explanatory that just trying to interpret source code)? Any links on where to learn this stuff and truly undertand it would be really welcome, and could help others in applying the core principles of this brilliant project to a wider variety of servo types and geometries.
Thank you

*particularly how you manage to make a DC motor behave as if it were proportional despite the fact that they typically won't move at all until some threshold PWM level is crossed and then they suddenly start moving quite fast

TTD1024, 2023-07-06:
Thank you.

That PWM compensation looks a very clever way to handle that problem simply and in a way which remains valid when having different torque demands on the servo.

I have not tried the PCB designs, I am more interested in understanding the underlying logic of your software so I can implement it with a different MCU type for use with different form factors of servo and other forms of encoder.

Thank you for your reply, I'll await seeing the extra documentation when it appears, thanks again for replying.

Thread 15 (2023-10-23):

Issue with bootloader

PointyyP, 2023-10-23:
After performing:

cd filename
sudo openocd

// I get "command not found"

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

smith901, 2023-10-24:
Looks like `openocd` isn't installed. Follow instructions [from this file in the project](https://github.com/adamb314/ServoProject/blob/main/PcbDesignes/ServoBrushed/burnBootloaderWithOpenOCD.txt).

PointyyP, 2023-10-24:
I was following the instructions and thought I installed openocd, but I'll give it a try again. Thanks!

PointyyP, 2023-10-24:
After installing openocd and soldering the three pins (D,C,Reset) I have a new error message after executing sudo openocd

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

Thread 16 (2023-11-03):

Maximum voltage of the brushed servo pcb

ShittyMetronome, 2023-11-03:
Hi !

Thank you for your incredible work, especially on making this project easy to make for everyone.

I have two questions regarding your custom pcb for brushed servos :
What is the maximum voltage allowed ? I would like to modify blue servos (ds3235 and ds3225) and power them with 2s batteries (8.4v max).
Does the modification change the max speed of the servo motor ? For example, I'd like to use blue ds3225 because of their speed (0.05s/60° @8.4v in theory).

Thank you !

Cydget, 2023-11-14:
Another option would be to change out the linear regulator with one that is rated for a higher voltage. You would need to make sure that the LDO/regulator does not exceed max power dissipation. Pd=(inputvoltage-3.3)*I_LDO. A good estimate for total LDO current is likely 100-150mA

ShittyMetronome, 2023-11-23:
Thank you both for your anwers !

Closed 2023-11-23.

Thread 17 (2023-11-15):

How did you measure the laser angle in the comparison? What was your setup in the video "How to make your servos awesome"?

PointyyP, 2023-11-15:
How did you obtain the data from the responses by the regular servos and the modded servos?
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

PointyyP, 2023-11-27:
Do you still have the data from a spreadsheet?

Closed 2024-01-05.

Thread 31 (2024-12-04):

Hardware questions

dominicklee, 2024-12-04:
Hi Adam,

Thank you for such a wonderful project! It is very impressive. I have ordered some PCBs from JLCPCB, as I am looking forward to building it and sharing my future build. I have some quick questions.

1. There are 3 empty holes, with what looks like a middle hole next to "Gain Mod". It is not populated with any component from BOM. What is Gain Mod for? Do we have to solder any component there or leave it open?

2. In your latest tutorial video, I saw that you soldered a little red wire from the middle pin to somewhere on the chip. Is that something I have to do, or is that just for testing?

3. There are 2 big holes near the motor driver chip. In your tutorial video, you did not show the motor terminals being soldered. I am assuming that the motor terminals should be soldered to those holes - am I correct?

4. In your video for the robot arm refilling a mechanical pencil, which software/firmware code did you use for the inverse kinematics? Is that open source? Did you design the gripper? If you don't mind, I would like to help you improve your project (to do more intelligent tasks) if you can guide me in creating a similar setup.

Also, I plan to design a top piece to enclose the PCB. Or do you already have a design for that too?

Thanks again!

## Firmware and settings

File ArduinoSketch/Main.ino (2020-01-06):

#undef max
#undef min

#include "ArduinoC++BugFixes.h"
#include "ThreadHandler.h"
#include "DCServo.h"
#include "Communication.h"

#include "config/config.h"

SET_THREAD_HANDLER_TICK(200);
THREAD_HANDLER_WITH_EXECUTION_ORDER_OPTIMIZED(InterruptTimer::getInstance());

ThreadHandler* threadHandler = ThreadHandler::getInstance();

class CommunicationHandler : public Communication
{
public:
    CommunicationHandler(DCServo* dcServo, unsigned char nodeNr, unsigned long baud) :
        Communication(nodeNr, baud),
        dcServo(dcServo)
    {
        Communication::intArray[0] = dcServo->getPosition() * 4;
        Communication::intArray[1] = 0;
        Communication::intArray[2] = 0;
        Communication::charArray[1] = 0;
        Communication::charArray[2] = 0;
    }

    ~CommunicationHandler()
    {
    }

    virtual void onReadyToSendEvent()
    {
    }

    virtual void onReceiveCompleteEvent()
    {
    }

    virtual void onErrorEvent()
    {
    }

    virtual void onComCycleEvent()
    {
        {
            ThreadInterruptBlocker blocker;

            Communication::intArray[3] = dcServo->getPosition() * 4;
            Communication::intArray[4] = dcServo->getVelocity();
            Communication::intArray[5] = dcServo->getControlSignal();
            Communication::intArray[6] = dcServo->getCurrent();
            Communication::intArray[7] = threadHandler->getCpuLoad();
            Communication::intArray[8] = dcServo->getLoopNumber();
            Communication::intArray[9] = dcServo->getMainEncoderPosition() * 4;
        }

        dcServo->onlyUseMainEncoder(Communication::charArray[2] == 1);

        dcServo->setReference(Communication::intArray[0] * 0.25, Communication::intArray[1], Communication::intArray[2]);

        if (Communication::intArrayChanged[0])
        {
            Communication::intArrayChanged[0] = false;
            dcServo->openLoopMode(false);
            dcServo->enable(true);
        }
        else if (Communication::intArrayChanged[2])
        {
            Communication::intArrayChanged[2] = false;
            dcServo->openLoopMode(true);
            dcServo->enable(true);
        }
        else
        {
            dcServo->enable(false);
        }
    }

    void onComIdleEvent() override
    {
        Communication::intArrayChanged[0] = false;
        Communication::intArrayChanged[2] = false;
        dcServo->enable(false);
    }

private:
    DCServo* dcServo;
};

std::unique_ptr<CommunicationHandler> communication;

void setup()
{
    communication = std::make_unique<CommunicationHandler>(DCServo::getInstance(), ConfigHolder::getCommunicationId(), 115200);

    threadHandler->enableThreadExecution();
}

void loop()
{
    communication->run();
}

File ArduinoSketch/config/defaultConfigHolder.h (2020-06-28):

#include <Eigen30.h>
#include "../EncoderHandler.h"
#include "../CurrentControlLoop.h"
#include "../OpticalEncoderHandler.h"
#include "../ArduinoC++BugFixes.h"
#include "../CommunicationHandlers.h"

#ifndef DEFAULT_CONFIG_HOLDER_H
#define DEFAULT_CONFIG_HOLDER_H

class DefaultConfigHolder
{
public:
    static std::unique_ptr<CurrentController> createCurrentController()
    {
        return std::make_unique<CurrentControlLoop>(400);
    }

    static std::unique_ptr<EncoderHandlerInterface> createOutputEncoderHandler()
    {
        return std::make_unique<EncoderHandler>(A5);
    }

    static std::unique_ptr<OpticalEncoderHandler> createMainEncoderHandler()
    {
        std::array<uint16_t, 512> aVec = {};
        std::array<uint16_t, 512> bVec = {};
        return std::make_unique<OpticalEncoderHandler>(aVec, bVec);
    }

    class DefaultControlParameters
    {
      public:
        static Eigen::Vector3f getKVector()
        {
            Eigen::Vector3f K;
            K << 0.0,
                0.0,
                0.0;

            return K;
        }

        static Eigen::Matrix3f getAMatrix()
        {
            Eigen::Matrix3f A;
            A << 1.0, 0.0, 0.0,
                0.0, 1.0, 0.0,
                0.0, 0.0, 1.0;

            return A;
        }

        static Eigen::Matrix3f getAInvMatrix()
        {
            Eigen::Matrix3f AInv;
            AInv << 1.0, 0.0, 0.0,
                0.0, 1.0, 0.0,
                0.0, 0.0, 1.0;

            return AInv;
        }

        static Eigen::Vector3f getBVector()
        {
            Eigen::Vector3f B;
            B << 0.0,
                0.0,
                0.0;

            return B;
        }

        static Eigen::Matrix<float, 5, 1> calculateLVector(uint8_t controllerSpeed, uint8_t backlashControllerSpeed,
                float dt, float a, float b)
        {
            float posControlPole = exp(-dt * controllerSpeed);
            float velControlPole[] = {exp(-1.0 * dt * 4 * controllerSpeed), exp(-0.9 * dt * 4 * controllerSpeed)};
    
            Eigen::Matrix<float, 5, 1> L;
            L[0] = (1.0 - posControlPole) / dt;
            L[1] = (a + 1 - velControlPole[0] - velControlPole[1]) / b;
            L[2] = (a - b * L[1] - velControlPole[0] * velControlPole[1]) / b;
            L[3] = 10 * L[2];
            L[4] = backlashControllerSpeed;

            return L;
        }

        static Eigen::Matrix<float, 5, 1> getLVector(uint8_t controllerSpeed, uint8_t backlashControllerSpeed)
        {
            float dt = getAMatrix()(0, 1);
            float a = getAMatrix()(1, 1);
            float b = getBVector()(1);

            return calculateLVector(controllerSpeed, backlashControllerSpeed, dt, a, b);
        }
    };
};

#endif

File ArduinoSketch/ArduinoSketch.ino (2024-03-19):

#include "src/ArduinoC++BugFixes.h"
#include "src/Hardware/ThreadHandler.h"
#include "src/Hardware/FailSafeHandler.h"

#include "config/config.h"

SET_THREAD_HANDLER_TICK(200);
THREAD_HANDLER_WITH_EXECUTION_ORDER_OPTIMIZED(InterruptTimer::getInstance());

ThreadHandler* threadHandler = ThreadHandler::getInstance();

std::unique_ptr<Communication> communication;

void setup()
{
    communication = ConfigHolder::getCommunicationHandler();
    threadHandler->enableThreadExecution();
}

void loop()
{
    FailSafeHandler::getInstance()->resetWatchdogTimer();
    communication->run();
}

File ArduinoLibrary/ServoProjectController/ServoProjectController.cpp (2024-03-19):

#include "ServoProjectController.h"

SerialCommunication::SerialCommunication(SerialComOptimizer serial, uint32_t timeout) :
        serial(serial), timeout(timeout)
{
}

SerialCommunication::SerialCommunication() :
        serial(nullptr), timeout(0)
{
}

void SerialCommunication::setNodeNr(unsigned char nr)
{
    nodeNr = nr;
}

void SerialCommunication::write(unsigned char nr, char value)
{
    commandArray.push_back(nr);
    commandArray.push_back(value);
}

void SerialCommunication::write(unsigned char nr, short int value)
{
    commandArray.push_back(nr + 64);
    commandArray.push_back(static_cast<unsigned char>(value));
    commandArray.push_back(static_cast<unsigned short>(value) / 256);
}

void SerialCommunication::requestReadChar(unsigned char nr)
{
    commandArray.push_back(nr + 128);
    receiveArray.push_back(nr);
}

void SerialCommunication::requestReadInt(unsigned char nr)
{
    commandArray.push_back(nr + 128 + 64);
    receiveArray.push_back(nr + 64);
}

char SerialCommunication::getLastReadChar(unsigned char nr)
{
    return charArray.at(nr);
}

short int SerialCommunication::getLastReadInt(unsigned char nr)
{
    return intArray.at(nr);
}

CommunicationError SerialCommunication::execute()
{
    unsigned char checksum = 0;
    unsigned char messageLenght = 0;

    checksum -= nodeNr;

    for (auto it = commandArray.begin(); it != commandArray.end(); ++it)
    {
        if (*it >= 128)
        {
            checksum -= *it;
            messageLenght += 1;
        }
        else if (*it >= 64)
        {
            checksum -= *it;
            ++it;
            checksum -= *it;
            ++it;
            checksum -= *it;
            messageLenght += 3;
        }
        else
        {
            checksum -= *it;
            ++it;
            checksum -= *it;
            messageLenght += 2;
        }
    }

    checksum -= messageLenght;

    serial.write(nodeNr);
    serial.write(checksum);
    serial.write(messageLenght);

    for (unsigned char byte : commandArray)
    {
        if (!serial.write(byte))
        {
            serial.sendWrittenData();
            serial.write(byte);
        }
    }
    serial.sendWrittenData();

    commandArray.clear();

    auto clearReceiveArrayAtExit = createCallAfterReturnHandler([this]()
        {
            this->receiveArray.clear();
        });

    unsigned char c = 0;
    bool error = false;
    for (auto it = receiveArray.begin(); it != receiveArray.end(); ++it)
    {
        error = !serial.read(c, timeout);
        if (error)
        {
            serial.read(c, timeout);
            return CommunicationError(nodeNr, CommunicationError::NO_RESPONSE);
        }

        if (*it == c)
        {
            if (*it >= 64)
            {
                error = !serial.read(c, timeout);
                if (error)
                {
                    serial.read(c, timeout);
                    return CommunicationError(nodeNr, CommunicationError::PARTIAL_RESPONSE_TYPE_1);
                }
                short value = c;

                error = !serial.read(c, timeout);
                if (error)
                {
                    serial.read(c, timeout);
                    return CommunicationError(nodeNr, CommunicationError::PARTIAL_RESPONSE_TYPE_2);
                }
                value += c * static_cast<unsigned short>(256);
                intArray.at(*it - 64) = value;
            }
            else
            {
                error = !serial.read(c, timeout);
                if (error)
                {
                    serial.read(c, timeout);
                    return CommunicationError(nodeNr, CommunicationError::PARTIAL_RESPONSE_TYPE_3);
                }
                charArray.at(*it) = c;
            }
        }
        else
        {
            while (true)
            {
                error = !serial.read(c, timeout);
                if (error)
                {
                    serial.read(c, timeout);
                    break;
                }
            }

            return CommunicationError(nodeNr, CommunicationError::UNEXPECTED_RESPONSE);
        }
    }
    error = !serial.read(c, timeout);
    if (error)
    {
        serial.read(c, timeout);
        return CommunicationError(nodeNr, CommunicationError::PARTIAL_RESPONSE_TYPE_4);
    }
    if (c != 0xff)
    {
        return CommunicationError(nodeNr, CommunicationError::CHECKSUM_ERROR);
    }

    return CommunicationError(nodeNr, CommunicationError::NO_ERROR);
}

DCServoCommunicator::DCServoCommunicator(unsigned char nodeNr, Communication* bus)
{
    activeIntReads.fill(true);
    activeCharReads.fill(true);
    this->nodeNr = nodeNr;
    this->bus = bus;

    communicationIsOk = false;
    initState = 0;
    backlashControlDisabled = false;
    newPositionReference = false;
    newOpenLoopControlSignal = false;

    setOffsetAndScaling(1.0f, 0);
}

void DCServoCommunicator::setOffsetAndScaling(float scale, float offset, float startPosition)
{
	this->scale = scale;
	this->offset = offset;
    this->startPosition = startPosition;

    if (isInitComplete())
    {
        updateOffset();
    }
}

void DCServoCommunicator::updateOffset()
{
    float pos = getPosition() / scale;
    startPosition /= scale;

    long int wrapSize = (1l << 24) / positionUpscaling;

    if (pos - startPosition > wrapSize / 2)
    {
        offset -= wrapSize * scale;
    }
    else if (pos - startPosition < -wrapSize / 2)
    {
        offset += wrapSize * scale;
    }
}

void DCServoCommunicator::setControlSpeed(unsigned char controlSpeed, float inertiaMarg)
{
    setControlSpeed(controlSpeed, controlSpeed * 4, controlSpeed * 32, inertiaMarg);
}

void DCServoCommunicator::setControlSpeed(unsigned char controlSpeed,
        unsigned short int velControlSpeed, unsigned short int filterSpeed,
        float inertiaMarg)
{
    this->controlSpeed = controlSpeed;
    this->velControlSpeed = velControlSpeed;
    this->filterSpeed = filterSpeed;
    inertiaMarg = stdmin::min(stdmin::max(inertiaMarg, 1.0f), 1.0f + 255.0f / 128);
    this->inertiaMarg = static_cast<unsigned char>(stdmin::round((inertiaMarg - 1.0f) * 128.0f));
}

void DCServoCommunicator::setBacklashControlSpeed(unsigned char backlashCompensationSpeed,
            float backlashCompensationCutOffSpeed,
            float backlashSize)
{
    this->backlashCompensationSpeed = backlashCompensationSpeed;
    this->backlashCompensationSpeedVelDecrease = static_cast<unsigned char>(stdmin::min(255.0f,
            255 * 10 / (backlashCompensationCutOffSpeed / stdmin::abs(scale))));
    this->backlashSize = static_cast<unsigned char>(backlashSize / stdmin::abs(scale));
}

void DCServoCommunicator::setFrictionCompensation(float fricComp)
{
    this->frictionCompensation = fricComp;
}


void DCServoCommunicator::disableBacklashControl(bool b)
{
    backlashControlDisabled = b;
}

bool DCServoCommunicator::isInitComplete() const
{
    return initState == 10;
}
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

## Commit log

2019-04-08 Renamed FilteredADC to CurrentSampler and removed filter constant parameter
2019-04-08 changed CurrentControlLoop implementation to simpler integer integral control
2019-04-09 Fixed bug in CurrentSampler init
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2019-04-09 Changed so that CurrentControlLoop getCurrent returns the filtered current
2019-04-09 Changed so that actual current is communicated instead of requested
2019-04-09 Changed so that both actual current and controlSignal is communicated
2019-04-09 fixed currentController active when control is disabled bug
    [DCServo.cpp]
2019-04-12 Implemented blockingRun version of communication run to fix race condition of communication->charArray[1] and changed thread parameters
    [Communication.cpp]
2019-04-12 Separated dotstar state indicator handling to separate thread
2019-04-12 fixed controlEnable init to true instead of false
    [DCServo.cpp]
2019-04-12 Fixed CurrentSampler::collect hanging
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2019-04-13 Changed so multiple threads can be executed in one interrupt to improve jitter
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2019-05-23 switched to delay thread codeBlock until implementation of currentController
2019-09-03 updated Encoder handler to handle the new AS5048A chip with higher resolution
2019-09-03 added start and done printout to compile and upload parts of makefile
2019-09-19 Switched counting direction of EncoderHandler after changing to AS5048A chip
2019-09-23 fixed changed array in Communication uninitialized bug
    [Communication.cpp]
2019-09-23 fixed initializing buffer instead of actual array problem in Communication
    [Communication.cpp]
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2019-10-16 made EncoderHandler give continues position output without wrap around (since Kalman filter needs continues values to work correctly)
    [EncoderHandler.cpp]
2019-10-16 fixed current loop gain problem (too high) when testing the new boards
    [CurrentControlLoop.cpp]
2019-10-16 fixed anti windup handling problems
    [CurrentControlLoop.cpp, DCServo.cpp]
2019-10-16 fixed problem with last communication frame being used as first after communication restart
    [Communication.cpp]
2019-10-16 moved encoder to motor shaft and updated control parameters
2019-10-20 Fixed continue after communication idle bug by implementing onComIdleEvent function
    [Communication.cpp]
2019-10-20 fixed bug in ReferenceInterpolator
    [DCServo.cpp]
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2019-11-05 replaced loop count on communication intArray[9] with motor position
    [DCServo.cpp]
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2019-12-19 Implemented use only motor encoder functionality and changed so getting motor encoder value has same unit as output encoder
2019-12-19 changed so that motor encoder sample triggering happens before current control loop execution (to optimize usage of adc when using optical encoder handler for motor encoder)
2019-12-19 Fixed type problem by adding vector size as a member of OpticalEncoderHandler
    [OpticalEncoderHandler.cpp]
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2020-01-04 Fixed only being able to disable servo by letting communication timeout
2020-01-04 fixed missing reset of uLimitDiff in disabled state
    [DCServo.cpp]
2020-01-04 added interrupt blocker to communication handler to guarantee all values come from same cycle
2020-01-06 Renamed encoder handlers and changed so outputEncoderHandler is optional
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2020-01-07 Added hardware related files for project
    [As5048aEncoderBoard.kicad_pcb, As5048aEncoderBoard.sch, MainPcb.kicad_pcb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]
2020-01-07 Renamed .ino file to fix compile error
    [ArduinoSketch.ino]
2020-01-10 added ability to disable backlash compensation
2020-01-14 Fixed Compile error in servoNr1 config
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2020-01-15 fixed backlash control disabling bug (writing to next node nr since after bus->execute();
2020-03-06 changed so filtered current value is updated in pwm mode
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2020-03-06 fixed casting to int bug for getMainEncoderPosition
    [DCServo.cpp]
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2020-03-06 Changed to optical encoder and changed gearbox of servoNr1
2020-03-06 updated a and b values for servoNr3 optical encoder
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2020-03-06 added support for pwm mode open loop control signal
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2020-03-15 fixed initialization bug in Communication
    [Communication.cpp]
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2020-03-15 routed backlashCompensation info to DCServoCommunicator
    [DCServo.cpp]
2020-03-15 Added option to get control error without backlash compensation
2020-03-16 fixed bugs related backlash compensation
    [DCServo.cpp]
2020-03-19 fixed filtered pwm not initialized bug
    [CurrentControlLoop.cpp]
2020-03-19 fixed memory leek in CurrentControlLoop
    [CurrentControlLoop.cpp]
2020-03-19 fixed filtered pwm value bug when in override pwm mode
    [CurrentControlLoop.cpp]
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2020-05-19 removed pwm output on D2 (PA14) and D5 (PA15) and renamed HBrideg4WirePwm
2020-05-19 Improved OpticalEncoderHandler noise handling (averaging multiple sensor samples and added cost for jittering angle)
    [OpticalEncoderHandler.cpp]
2020-05-19 replaced forgotten hard coded vector size of opticalEncoderHandler
    [OpticalEncoderHandler.cpp]
2020-05-19 implemented 32 times upscaling of position integer value to reduce quantization noise (previous upscaling was 4 times)
    [CommunicationHandlers.cpp, CommunicationHandlers.h]
2020-05-19 fixed backlashComponsation scaling bug
2020-05-19 implemented harder communication timing that is robust against master cycle time jitter (master may be executing on non-real time operating system with high timing jitter)
    [CommunicationHandlers.cpp, DCServo.cpp]
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2020-05-19 Decreased backlash compensation control parameter
2020-05-21 fixed white spaces in Communciation.cpp
    [Communication.cpp]
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2020-06-22 updated and organized cad files and pcb designs
    [As5048aEncoderBoard.kicad_pcb, As5048aEncoderBoard.sch, Gripper.FCStd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]
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2020-06-28 Replaced missing Eigen repo
    [defaultConfigHolder.h]
2020-06-29 Removed extra OpticalEncoder folder
    [OpticalEncoder.kicad_pcb, OpticalEncoder.sch]
2020-06-29 added backlash section to readme
2020-06-30 cleaned up text positions in As5048aEncoderBoard schematic
    [As5048aEncoderBoard.sch]
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2020-07-04 fixed wrong connection pin names for Optical encoder schematic
    [OpticalEncoder.sch]
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2020-07-10 Implemented new backlash compensation control
    [CommunicationHandlers.cpp, DCServo.cpp, defaultConfigHolder.h]
2020-07-10 fixed problems with offset calculation being done after servo init. (scale is not set before setBacklashControlSpeed)
2020-09-20 Fixed sign handling bug in CurrentControlModel
    [CurrentControlLoop.cpp]
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2020-10-09 fixed unique_ptr moved bug in constructor
    [CommunicationHandlers.cpp]
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2020-10-09 improved backlash compensation
2020-10-09 added washer to gripper CAD
    [Gripper.FCStd]
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2021-02-23 fixed negative scale bug for backlash control parameters
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2021-02-23 updated servo control parameters after finding bug in systemIdent script
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2021-03-22 fixed ringing pwm when brake is active for HBridge2WirePwm
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2021-04-11 Fix for new version of Arduino adding define for abs, which breaks c++ stl
    [ArduinoSketch.ino]
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2021-04-11 added readout of high bits of main encoder position (needed for encoder calibration)
2021-04-11 added missing ResistiveEncodrHandler include to defaultConfigHolder
    [defaultConfigHolder.h]
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2021-04-12 fixed dynamic kalman filter speed bug
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2021-04-21 Updated cad files
    [Gripper.FCStd, GripperBase.stl, GripperClip.stl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]
2021-04-21 updated schematics and PCB
    [As5048aEncoderBoard.kicad_pcb, MainPcb.kicad_pcb, MainPcb.sch]
2021-04-26 Added noise to optical encoder channels for simulation
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2021-04-26 added handling of inverted output encoder
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2021-04-26 added optical encoder wheel dimensions images
    [MicroServoAssembly.FCStd, motorLid.FCStd]
2021-05-22 Fixed bug in reference timing when switching from open loop to closed loop mode and improved timing implementation
    [CommunicationHandlers.cpp, DCServo.cpp]
2021-05-22 optimized for short cycle time
    [ArduinoSketch.ino, DCServo.cpp, OpticalEncoderHandler.cpp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]
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2021-05-29 fixed array initialization on each loop bug for pwm comp function
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2021-05-29 lowered relative kalman filter speed to suppress noise
    [DCServo.cpp]
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2021-06-27 improved noise resilience for optical encoder calibration
2021-06-27 updated 3D models and added servo covers
    [GripperMount.stl, ServoBigMagEnc.stl, ServoBigMagEncMagHold.stl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]
2021-09-03 Added support for advanced control parameters to communication (vel control loop and filter speed)
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2021-09-03 Implemented SwitchAvoidingSynchronizer to limit noise of analog encoders
    [OpticalEncoderHandler.cpp, ResistiveEncoderHandler.cpp]
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2021-11-06 Moved Servo design files to ServoCoreless folder
    [As5048aEncoderBoard.kicad_pcb, As5048aEncoderBoard.sch, MainPcb.kicad_pcb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]
2021-11-06 Added Brushed servo design files
    [EncDisc.stl, EncDiscBack.stl, backCover.FCStd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]
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2021-11-06 increased switch avoiding transient time for HBridgeHighResPin11And12Pwm
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2021-11-07 Replaced loopNumber counting with loopTime measured in us
    [CommunicationHandlers.cpp, DCServo.cpp]
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2021-12-26 updated version of ServoBrushed combined pcb
    [combined-B_Cu.gbl, combined-B_Mask.gbs, combined-B_Paste.gbp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]
2021-12-26 sorted ServoBrushed combined pcb manufacturing files
    [combined-B_Cu.gbl, combined-B_Mask.gbs, combined-B_Paste.gbp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]
2021-12-27 updated version of 3D printed parts for Servo Brushed
    [EncDiscBlack.stl, EncDiscWhite.stl, backCover.FCStd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]
2021-12-27 Added PrusaSlicer printing project for Servo brushed
    [PrusaMiniPrintProject.3mf]
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2022-02-15 Changed to ArduinoEigen lib in standard Arduino library list (under name 'Eigen')
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2022-02-15 fixed port change not detected bug in ConfigurationGui script
    [ConfigurationGui.py, OpticalEncoder.py, OutputEncoder.py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]
2022-02-15 fix for writeInt with small negative value resulting in byte overflow
    [Communication.py]
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2022-02-15 Added end limit avoiding function to optical encoder calibration + code cleanup
    [GuiHelper.py, OpticalEncoder.py]
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2022-02-15 added end limit avoiding function to system identification and configurable dt
    [SystemIdentification.py]
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2022-02-19 new print settings for brushed servo 3D printed parts
    [PrusaMiniPrintProject.3mf]
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2022-02-22 Increased hole size for cables in ServoBrushed backCover
    [PrusaMiniPrintProject.3mf, backCover.FCStd, backCover.stl]
2022-02-23 Added create missing directories functionality to makefiles and configuration scripts
    [ArduinoManager.py, ConfigurationGui.py]
2022-02-24 fixed bug in OutputEncoderCalibrationGenerator
    [OutputEncoder.py]
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2022-02-26 fixed Python and C++ lib implementation for encoder multi-turn handling (see commit 603abec65cd1ff277f2ffd3473fd13ea201ecbc9)
    [Communication.py]
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2022-04-14 fixed missing update of dtDiv2 in ReferenceInterpolator.updateTiming()
    [DCServo.cpp]
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2022-08-07 updated ReferenceInterpolator to be zoh correct
    [DCServo.cpp]
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2022-08-17 Improved python servo simulation and added unittest for communication.py
    (cherry picked from commit d169f6f28a8a594ac4e1f6f64f992ce8edd6c1d5)
2022-08-17 fixed pylint errors and warnings
    [ArduinoManager.py, Communication.py, ConfigurationGui.py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]
2022-08-18 fix bugs in dependency handling
    [ArduinoManager.py, DependencyHandler.py, Helper.py]
2022-08-19 fixed regex line break bug
    [MotorCoggingTorque.py]
2022-08-19 fixed missing time unit scaling when setting outputModelDt
    [SystemIdentification.py]
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2022-11-13 fixed missing rounding in DCServoCommunicator
    [Communication.py]
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2022-11-13 added simulated scaling error for rawOutputPos in DCServo
    [DCServo.cpp]
2022-11-13 fixed error in calculating dt
    [SystemIdentification.py]
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2022-12-05 optimized implementation of pwmHighFrqCompFun with fixed point calculation
    [Helper.py]
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2022-12-30 fixed unstable feedback buck for posRefTamingOffset for openLoopControlMode
    [DCServo.cpp]
2022-12-30 optimized EncoderHanlder compVec calculation (changed to fixed point math)
    [EncoderHandler.cpp]
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2023-03-30 Fixed pylint warnings and pytest tests
    [Helper.py, SystemIdentification.py]
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2023-06-17 optimized backlash control gain calculation
    [DCServo.cpp]
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2023-06-24 Fixed bugs related to defaultSim.h config commit: 19083a8c3e797b1c3afdb0e01f51001b7514f4e1
    [ConfigurationGui.py, Helper.py, OutputEncoder.py]
2023-06-24 changed noise levels on python simulation
    [Communication.py]
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2023-06-26 changed to fixed point implementation of SimulationHandler
    [SimulationHandler.cpp]
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2023-06-26 fixed bug in OutputEncoder calibration
    [OutputEncoder.py]
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2023-06-26 new version of EncoderDiscWhite.stl
    [EncDiscWhite.stl, PrusaMiniPrintProject.3mf, motor.FCStd]
2023-06-27 changed to fixed point implementation of CurrentControlModel
    [CurrentControlLoop.cpp]
2023-06-29 Fixed corruption in part MotorLid of ServoBrushed motor cad
    [motor.FCStd]
2023-07-06 fixed casting warning in CurrentControlModel
    [CurrentControlLoop.cpp]
2023-07-06 fixed getModelDtFromConfigFileString bug for contineusA == 0.0
    [SystemIdentification.py]
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2023-07-06 improved motorLid part of ServoBrushed
    [PrusaMiniPrintProject.3mf, motor.FCStd, motorLid.stl]
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2023-07-07 Fixed ServoBrushed PCB EMI problem
    [combined-B_Cu.gbl, combined-B_Mask.gbs, combined-B_Paste.gbp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]
2023-07-07 fixed new pylint version warnings
    [ArduinoManager.py]
2023-07-08 new ServoBrushed PCB
    [combined-B_Cu.gbl, combined-B_Mask.gbs, combined-B_Paste.gbp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]
2023-07-22 PWM damping (brake instead of H-bridge off for idle part of PWM cycle) based friction compensation
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2023-07-23 better noise handling in OpticalEncoder.py by sorting channel sum and diff
    [OpticalEncoder.py]
2023-07-23 fixed bug in OpticalEncoder.py sensor weights
    [OpticalEncoder.py]
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2023-07-23 improved stability of SystemIdentification.py simulation
    [SystemIdentification.py]
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2023-07-23 fixed python linting warnings
    [Communication.py, MotorCoggingTorque.py, OpticalEncoder.py]
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2023-10-07 fixed compiler error for ArduinoLibrary
    [ServoProjectController.cpp]
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2023-10-07 fixed saying "No" on "plot the recorded data" dialog bug for MotorCoggingTorque.py
    [MotorCoggingTorque.py]
2023-10-07 implemented filtering of opticalEncoder calibration to remove stochastic sampling noise
    [OpticalEncoder.py]
2023-10-07 fixed pylint and python tests warnings
    [MotorCoggingTorque.py, OpticalEncoder.py]
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2023-10-14 fixed problem with some MessageDialogs created outside main thread
    [MotorCoggingTorque.py, OpticalEncoder.py, OutputEncoder.py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]
2023-10-14 fixed rounding error for neg comp values in ResistiveEncoder
    [ResistiveEncoderHandler.cpp]
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2023-10-14 fixed showAdditionalDiagnosticPlots for when oldAVec is None
    [OpticalEncoder.py]
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2023-12-11 bug workarounds for matplotlib
    [Helper.py]
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2023-12-11 fixed bug in OutputEncoder.py plot generated vector
    [OutputEncoder.py]
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2024-02-22 less noise sensitive Optical encoder calibration
    [OpticalEncoder.py]
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2024-02-22 changed so threads can re-trigger straight away if time until run has passed
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2024-02-22 added missing step files for robot2 cad
    [brushedServo.step, brushedServoHorn.step, microServo.step]
2024-03-18 Completed 'No motor surgery' version and made it the new default with updated DOC
    [As5048aEncoderBoard.kicad_pcb, As5048aEncoderBoard.sch, EncDiscBlack.stl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]
2024-03-19 Fixed lintPythonCode and runPythonTests warnings and errors
    [GuiHelper.py, Helper.py, OpticalEncoder.py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]
2024-03-19 Fixed output encoder comp list too short bug
    [OutputEncoder.py]
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2024-03-19 Added better description of min and max pwm values for systemIdentification.py and changed to pwm step size to 1 for opticalEncoder.py
